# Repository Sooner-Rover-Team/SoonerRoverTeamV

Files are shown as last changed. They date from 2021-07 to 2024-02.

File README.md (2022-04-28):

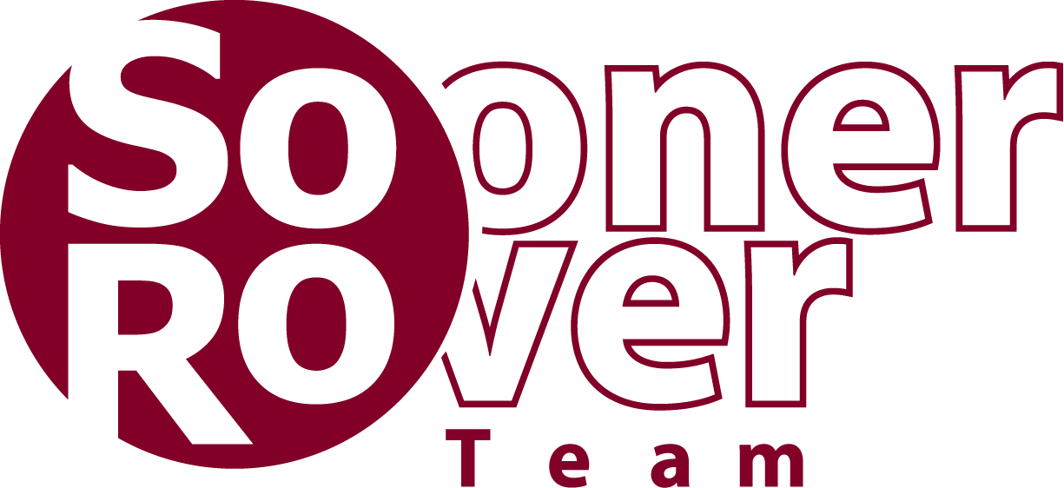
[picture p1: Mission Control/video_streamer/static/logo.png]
Sooner Rover Team Logo


---

This is the current code repository for the Sooner Rover Team.

## Active Tasks
[CS Tasks](https://github.com/bentonsmith8/SoonerRoverTeamV/projects/2)

[Electrical Tasks](https://github.com/bentonsmith8/SoonerRoverTeamV/projects/3)

## Previous Repo
[Link to the SoRo-19-20 Repo](https://github.com/eric-plus-plus/SoRo-19-20)

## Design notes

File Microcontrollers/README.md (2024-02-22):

# Microcontrollers
This folder contains all microcontroller code that has been used on SORO in the past. Some examples are provided for testing. The current implementation is in the Teensy 4.1 folder.

## Message Structures
### UDP
Mission Control sends UDP msgs to Ebox, which can also send CAN msgs to Arm/Science. UDP sends byteArrays, so assume each value is 0-255
- To Wheels = [0x01, 0x01, wheel0, wheel1, wheel2, wheel3, wheel4, wheel5, checkSUm]
- To LEDs = [0x01, 0x02, r, g, b, checkSum]
- To Arm = [0x02, bicep, foreArm, base, wristPitch, wristRotate, claw, checkSum]
- To Science = [0x03, bigAct, smallAct, testTubeAct, drill, servoCam, checkSum]
### CAN
Teensy microcontrollers communicate with each other via CAN (Ebox, 2 Arm and 1 Science). ID of CAN msg sets priority, meaning ID=0x03 has to wait for ID=0x01 to finish sending messages on the bus
- To lowerArm: ID = 0x01
- To upperArm: ID = 0x02
- To Science: ID = 0x03
- Back to Ebox = 0x04

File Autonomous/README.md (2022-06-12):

# Autonomous Code
This folder contains all of the code needed for the autonomous program to run. We tied for 2nd in the 2022 autonomous course with this code when one of our wheels wasn't moving!

## Dependencies
Requires `opencv-contrib-python` to be installed
Run `pip3 install .` in this folder <br>

## Running
First, ensure that `main.py` drives to the desired ArUco markers <br>
To run the main autonomous program without awful debugging output, enter
`python3 main.py <camera_file> 2> /dev/null` <br>
* To get the camera file, enter `v4l2-ctl --list-devices` to find the desired camera's file. It will look like `/dev/video2` <br>
<br>
To view the rover's location and get coordinates, navigate to &lt;rover's ip&gt;:5000 in your web browser

## Code Structure
### main.py
This is the program that gets run. This program allows the user to enter in GPS coordinates and then drives to the specified tags with -1 being given for a waypoint with no tag.

### Drive.py
The Drive class gives the user the ability to travel to a set of GPS locations while looking for a tag and then track either a tag or a gatepost after they've been seen.

### Location.py
API for using the GPS. Has methods that allows us to easily get the rover's heading and find how far the rover is from a set of GPS coordinates.

### UDPOut.py
Functions that allows the autonomous code to easily communicate to the MBed to control the wheels and LEDs.

### ARTracker.py
Class that gives the rover the ability to see ArUco markers and gets the rover's angle and distance from them. Also has the ability to utilize YOLO for the same purpose if the environment is properly setup.

### findFocalLength.py
Run this program directly to figure out the FOCAL_LENGTH parameters in config.ini

### gps
This folder contains the code needed to talk to the Swift GPS modules. I don't recommend going in here.

### runAutonomous.sh
Depricated. Can probably delete this but keeping it incase y'all ever go back to using three cameras

## Previous Code
Link to old, c++ autonomous code: https://github.com/eric-plus-plus/SoRo-19-20/tree/master/Autonomous

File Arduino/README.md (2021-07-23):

# Arduino Code :100:

Required libraries (install them from the built in library manager):
* EtherCard (1.1.0)
  * Only needed for using the Arduino Nano ethernet shield. The Uno-style shield (on the Megas) uses the built in ethernet library.
  * [GitHub](https://github.com/njh/EtherCard)

The "capstone arm" folder is full of other Arduino programs that were indended for the belt driven arm we did not end up using.

## Testing Programs

### servo_test.ino

This program is good for calibrating/testing a single talon (our motor controller).
To use it, change `#define PIN_SERVO 31` to whatever Arduino pin you're connecting the signal wire to, upload the code, and then open the serial monitor.
When you send a number to the Arduino it will write it to the servo.
When calibrating, use the range 10 to 170 instead of the full 0 to 180 because it freaks out the talons. 90 degrees will be still.

## Rover Programs

### wheel_controller.ino

This should be uploaded to the Arduino Nano in the e-box. The macro `#define DEBUG_MODE 0` can enable serial debugging messages. Don't use this when running the rover because it can cause the Arduino to randomly reset.

### arm_controller.ino

This is the code for the Arduino Nano controlling the currently used arm (the one with linear actuators). Like the wheel controller, it also has the optional debug macro.

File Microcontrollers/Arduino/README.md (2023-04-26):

# Arduino Code :100:

### mostRecent
    contains the arduino code that was last used on the rover before switching to Teensy.

### past_code 
    contains any program someone has made in the past for arduino that is no longer in use.

### examples 
    contains test scripts designed to make testing motors and arduino accessories easy.

Required libraries (install them from the built in library manager):
* EtherCard (1.1.0)
  * Only needed for using the Arduino Nano ethernet shield. The Uno-style shield (on the Megas) uses the built in ethernet library.
  * [GitHub](https://github.com/njh/EtherCard)

<!-- ## Testing Programs

### servo_test.ino

This program is good for calibrating/testing a single talon (our motor controller).
To use it, change `#define PIN_SERVO 31` to whatever Arduino pin you're connecting the signal wire to, upload the code, and then open the serial monitor.
When you send a number to the Arduino it will write it to the servo.
When calibrating, use the range 10 to 170 instead of the full 0 to 180 because it freaks out the talons. 90 degrees will be still.

## Rover Programs

### wheel_controller.ino

This should be uploaded to the Arduino Nano in the e-box. The macro `#define DEBUG_MODE 0` can enable serial debugging messages. Don't use this when running the rover because it can cause the Arduino to randomly reset.

### arm_controller.ino

This is the code for the Arduino Nano controlling the currently used arm (the one with linear actuators). Like the wheel controller, it also has the optional debug macro. -->

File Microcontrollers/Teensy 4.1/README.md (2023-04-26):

# Teensy
Teensy 4.1 microcontrollers are currently installed on REMI. They have a very high clock speed and built-in CAN tranceivers.

## REMI Setup
The teensyEBOX program receives UDP messages from the manual_operate.py program in MissionControl. Depending on the message contents, the teensy will either update wheel speeds/LEDs, or send CAN messages to the arm/ science package. The arm contains two teensy 4.1 microcontrollers so two CAN messages are sent to the arm at a time. The arm could be ran with one Teensy but eventually encoders will be added which could lead to input delay.

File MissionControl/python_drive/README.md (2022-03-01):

# manual_operate

This code can drive the rover, move the arm, and operate the science package.

## Usage

The config.ini file must have the correct ip addresses of the microcontrollers.

Ebox MBED IP: 10.0.0.101
Ebox MBED Port: 1001
Arm Arduino IP: 10.0.0.102
Arm Arduino Port: 1002
Science Arduino IP: 10.0.0.103
Science Arduino Port: 1003

The controller configuration can also be adjusted as different axes will have different indicies depending on the system/controller.
Config **0** sets the dual sticks to axes 0-3 while the triggers are 4 and 5. Config **1** sets left axes to 0 and 1 with the left trigger set to 2. The right stick is set to 3 and 4 with the right trigger at 5. To figure out the mappings of the controller, run controllertester.py.

## Controls

There are two distinct modes in the program: drive and operate. Drive obviously just drives the wheels. Operate can be used to control either the science package or the arm, depending on which is installed (can be toggled by pressing **Select**). **B** switches between drive and operate.

### Drive

The rover drives with tank controls (**Left Stick** moves left wheels, **Right Stick** moves right wheels). The **Left Bumper** will only move the front wheels while the **Right Bumper** will only move the back wheels. This could be useful for getting the rover unstuck. **A** will just make the lights flash. 

### Arm

The arm is controlled with the help of the GUI. The **Left Stick** controls the point of the wrist in space and the actuators will automatically adjust their length to keep the wrist on that point. The **Right Stick** controls the tilt and rotation of the wrist. The operator must be careful not to overtwist the wrist as the cords can get tangled and disconnected if the wrist is rotated too far. **A** opens and closes the claw. **Left Trigger** rotates the base to the left while **Right Trigger** rotates the base to the right.

### Science Package

The Science package has 4 distinct controllable elements. The **Left Stick** moves the drill up and down in space. The **Right Stick** controls the speed of the drill. **Right Trigger** increases the speed of the vacuum while **Left Trigger** decreases it. **Left Bumper** rotates the carousel clockwise while **Right Bumper** rotates the carousel counterclockwise. **A** attempts to move the carousel one seventh of a rotation, but it is based on time elapsed and may not move the same amout each time.

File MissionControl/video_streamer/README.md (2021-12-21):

# RoverCam Python

The video streamer is written in python. It requires python3 version >=3.8.5, 4 libraries, and creation of a virtual environment.

## Setting Up A Virtual Environment

Linux only: install virtual environments with

```bash
sudo apt-get install python3-venv
```

Make sure you are in /SoRo-19-20/Mission Control/video_streamer/ then run

```bash
python3 -m venv .venv
```

This will create a new virtual environment in /video_streamer/. The virtual environment must be activated every time the program needs to be run which can be done with:

Linux:

```bash
source .venv/bin/activate
```

Windows (Powershell):

```powershell
.venv/Scripts/Activate.ps1
```

---

## Installing Packages

Next, these four packages need to be installed

- wheel
- imutils
- flask
- opencv-contrib-python

install these with

```bash
python3 -m pip install wheel opencv-contrib-python flask
```

The imutils package needs to be installed after wheel:

```bash
python3 -m pip install imutils
```

---

## Usage

To run, use

```bash
python3 client.py -i [ip of the device] -o [port] --resolution "{width}x{height}" --source 1,2,3
```

and navigate to that ip from another device.

### Notes on Usage

The program will automatically look for up to 10 cameras on launch, but only 3 simultaneous streams are supported for bandwidth considerations. Additionally, specific camera indices can be specified through an argument. 

The resolution of cameras can be set via an argument. The default resolution is 640 by 480 but any resolution can be set by passing in a string such as "1280x720". "max" can also be passed as a resolution to set the cameras to their maximum resolution. Recordings from each camera can be started and will be saved to ./recordings/recording.avi. The quality and framerate can both be adjusted during runtime.

Each stream can also be relaunched, which disposes of the current VideoCapture and VideoWriter object and creates new instances. This could be useful in case of a hardware error with a USB camera; the program can reaccess the camera without fully restarting. It also has the side effect of saving any recordings that had been captured up to that point in the execution.

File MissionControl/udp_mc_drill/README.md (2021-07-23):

# Drill Controller
 ## Bindings
 Actuator - Left stick Y axis

 Fan speed - A/B (South/East) buttons to accelerate and decelerate, 
 respectively

 Drill speed - X/Y (West/North) buttons to accelerate and decelerate, respectively

 Front triggers (left or right doesn't matter) - Reset fan speed

 Back triggers (left or right doesn't matter) - Reset drill speed

 Direction - Bound to DPad buttons. Up for 1, right for 2, released for 0.

 # Running without compiling
 There's a chance your system can just run the binary in `/target/release/drill_controller`

 If you cannot you need to...
 # Compile from source and run
 Following the steps on [the Rust-lang website](https://www.rust-lang.org/tools/install), 
 execute 

```shell
curl --proto '=https' --tlsv1.2 -sSf https://sh.rustup.rs | sh`
```

and do what it says to

Once rust is installed, you can execute `cargo run` from the `/udp_mc_drill` directory (the `Cargo.toml` file *must* be in the directory you execute `cargo run` from, which is why you need to be in `/udp_mc_drill` to run it).

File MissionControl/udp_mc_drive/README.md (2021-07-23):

# Remote Control
This is a newer remote control program written in Rust.
Rust was chosen with the hopes that dependency management would be way easier than the issues that Python created.

# Building - Requires Rust to be installed
To build the program, execute `$ cargo build --release`.
The binary will be placed in `./target/release/rover_controller`.
You can run that binary as normal or execute `$ cargo run` to build and run all in one step

# Running the prebuilt binary
This repository tracks the `target` directory as I develop and test the program. This means that there is a prebuilt binary in the target directory.
While building for development, the binary is built at `./target/debug/rover_controller`, so this location will always be the latest revision. `./target/release/rover_controller` includes a binary with some compiler optimizations and such, which may or may not be desirable. It's a better bet to run the executable in the `./target/debug/` directory because the executable in `./target/release/` will only be built if I remember to build it, and the `./target/debug/` directory will have the binary whether I remember or not.

# Configuration
The config file only needs a single line, in the format
`target=[ARDUINO_IP]:[PORT]`. If the config file is missing or malformed, a default will be used. This default is (as of v0.9.0) `target=192.168.1.101:1237`, which should work with the arduino as it stands at the time of writing.

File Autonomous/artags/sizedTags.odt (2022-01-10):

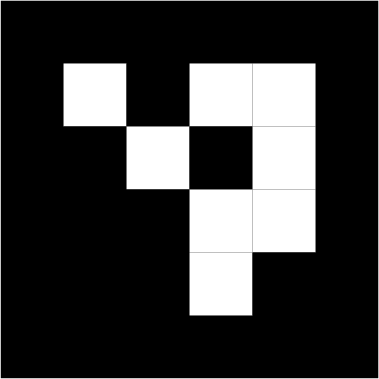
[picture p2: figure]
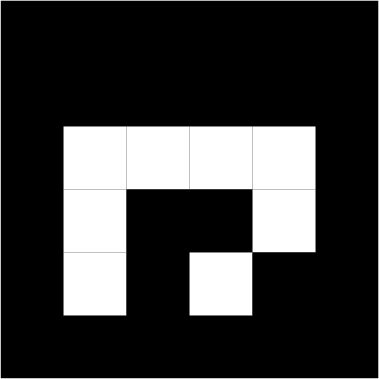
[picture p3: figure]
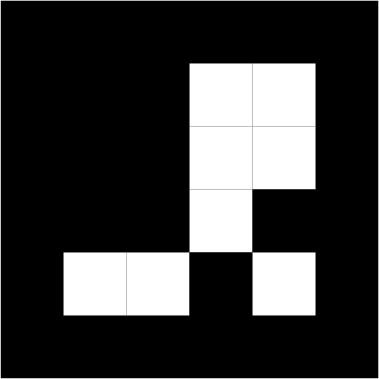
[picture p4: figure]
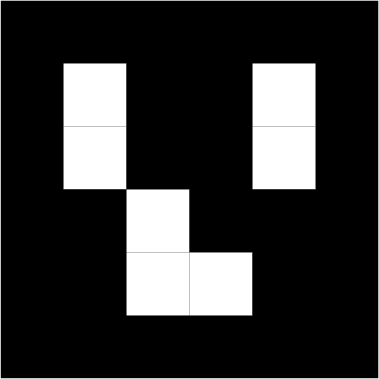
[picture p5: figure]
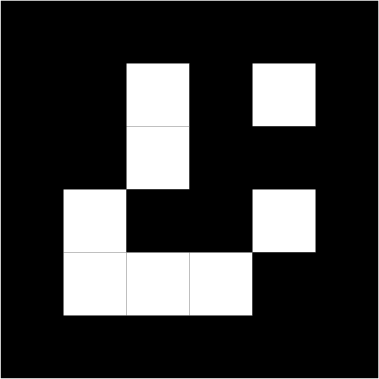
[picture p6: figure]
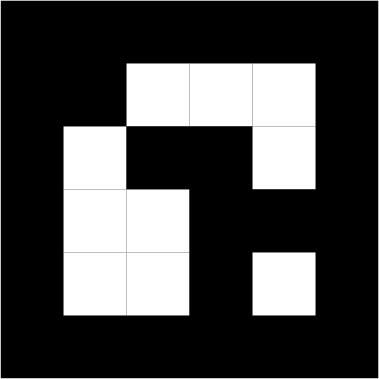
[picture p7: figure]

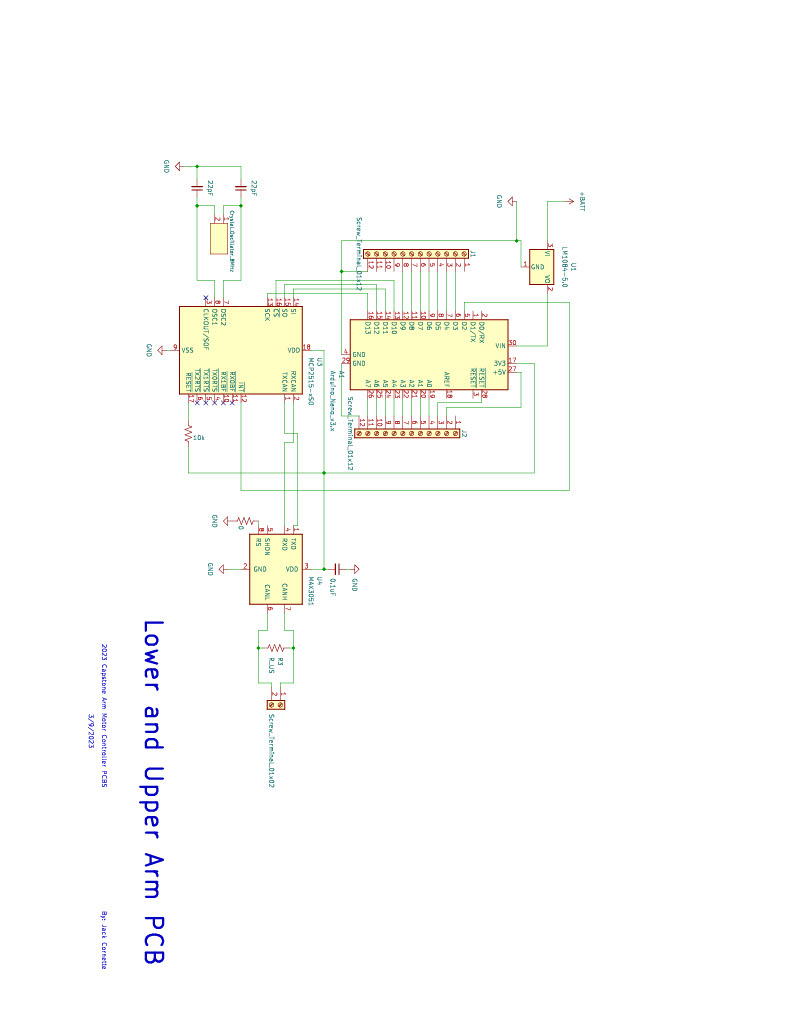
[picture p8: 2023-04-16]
PCB/Arm/lowerArm_upperArm/schematicPDF1024_1.jpg

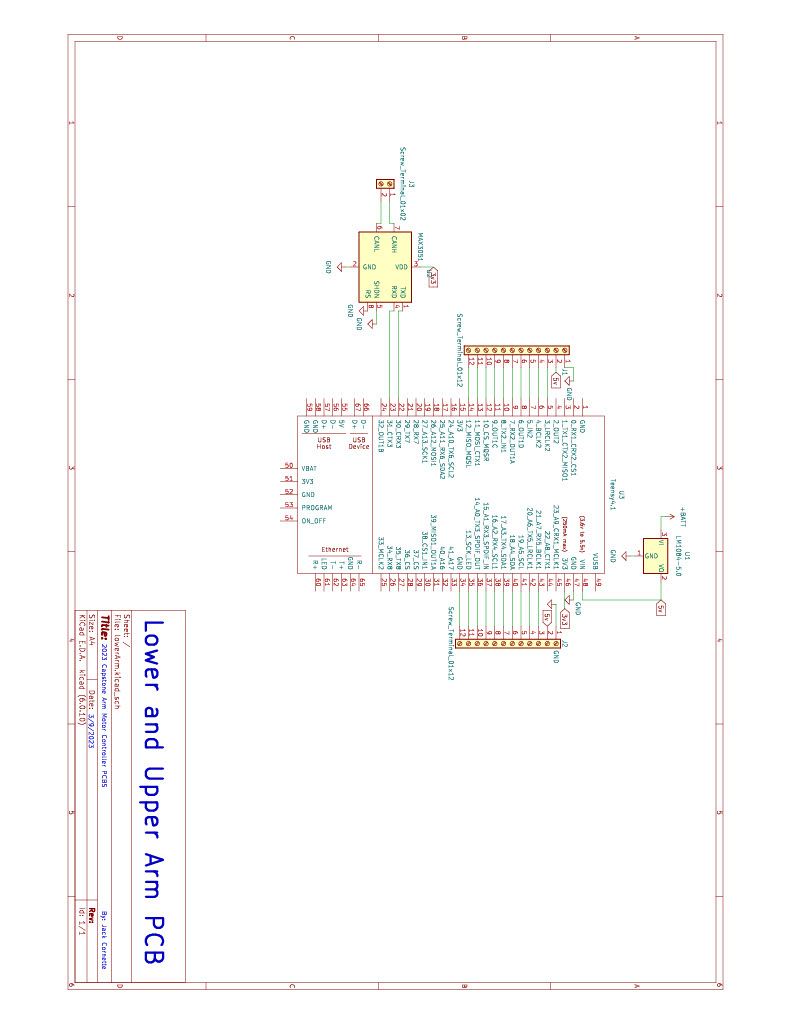
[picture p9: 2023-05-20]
PCB/Arm/teensyLowerUpperArm/schematic.jpg

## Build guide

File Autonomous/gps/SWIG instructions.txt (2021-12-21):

In order to run SWIG you must:
install swig
install python dev tools
make sure you have gcc/g++ installed
create interface files module.i

Process:
1. wrap edc.c into a library
2. use edc.c to wrap sbc.c into a library
3. use sbc.c to wrap gps.c into a library
4. Then use gps.c library to wrap main.c or main.cpp

=================REWRAPPING INSTRUCTIONS================
to wrap edc.c:

swig -python edc.i
gcc -fpic -c -I/usr/include/python3.8 edc.c edc_wrap.c
gcc -shared edc.o edc_wrap.o -o _edc.so
python3
import edc

----- It seems to work
============================================================================
to wrap sbp.c:

swig -python sbp.i
gcc -fpic -c -I/usr/include/python3.8 sbp.c sbp_wrap.c
gcc -shared sbp.o sbp_wrap.o -o _sbp.so edc.o 
python3
import sbp

---- It seems to work too, adds edc.o to the linking step so that it can get the edc functions
========================================================================================
To wrap gps.c:

swig -python gps.i
gcc -fpic -c -I/usr/include/python3.8 gps.c gps_wrap.c
gcc -shared gps.o gps_wrap.o -o _gps.so sbp.o edc.o
python3
import gps

--- Seems to work
==================================================================================
To wrap main.c:

swig -python main.i
gcc -fpic -c -I/usr/include/python3.8 main.c main_wrap.c
gcc -shared main.o main_wrap.o -o _gpsmain.so gps.o sbp.o edc.o
python3
import gpsmain
gpsmain.gpsmain()

--- Seems to work without the connection, though, just prints 0s for all the results
==========================================================================================

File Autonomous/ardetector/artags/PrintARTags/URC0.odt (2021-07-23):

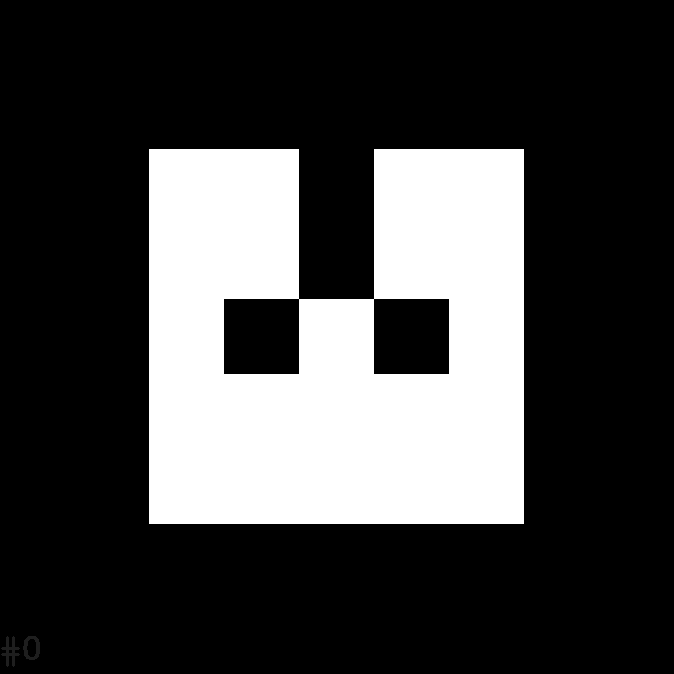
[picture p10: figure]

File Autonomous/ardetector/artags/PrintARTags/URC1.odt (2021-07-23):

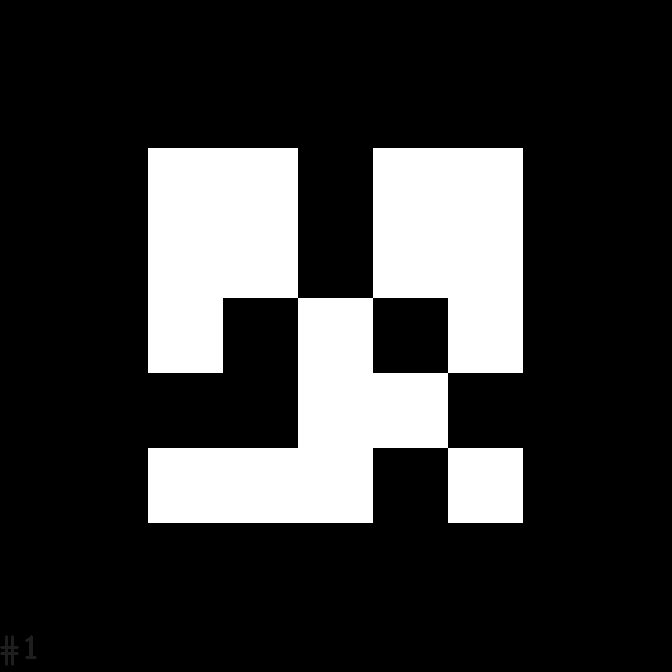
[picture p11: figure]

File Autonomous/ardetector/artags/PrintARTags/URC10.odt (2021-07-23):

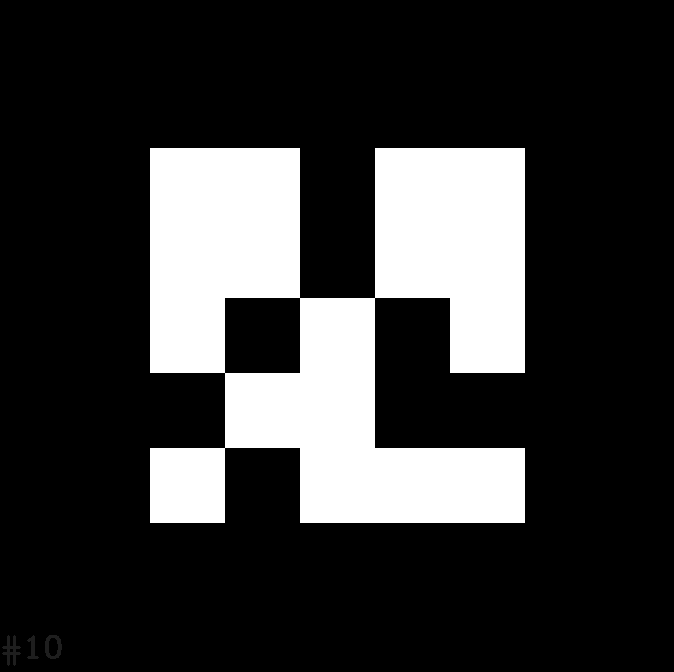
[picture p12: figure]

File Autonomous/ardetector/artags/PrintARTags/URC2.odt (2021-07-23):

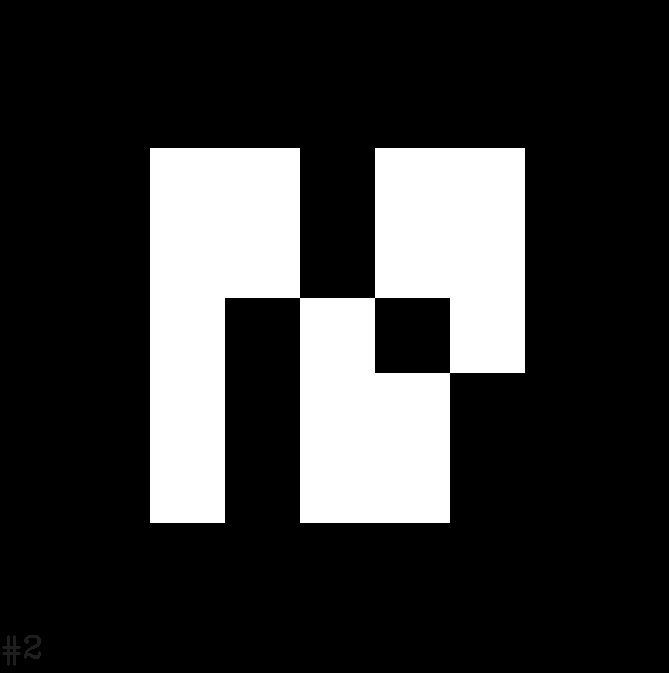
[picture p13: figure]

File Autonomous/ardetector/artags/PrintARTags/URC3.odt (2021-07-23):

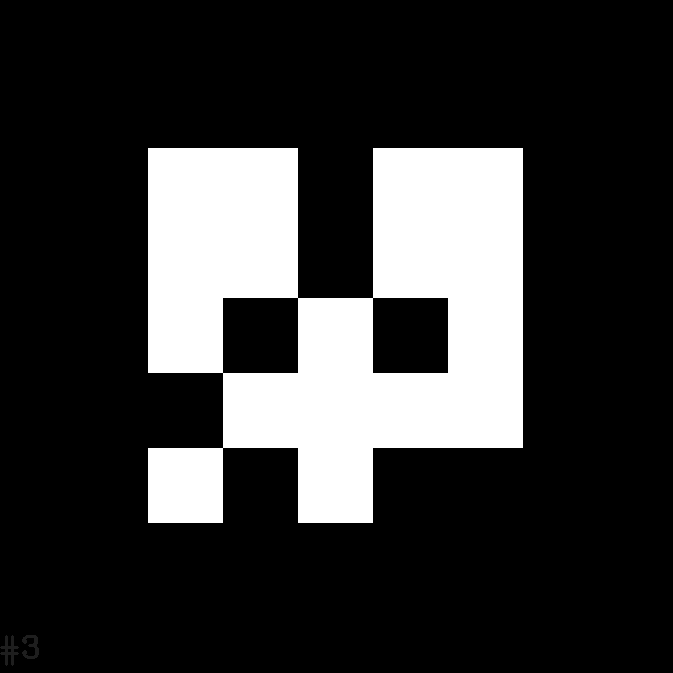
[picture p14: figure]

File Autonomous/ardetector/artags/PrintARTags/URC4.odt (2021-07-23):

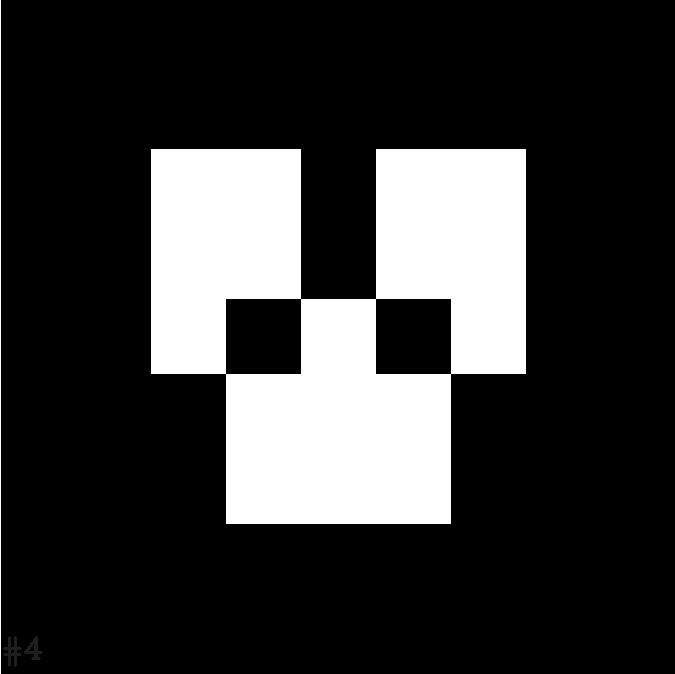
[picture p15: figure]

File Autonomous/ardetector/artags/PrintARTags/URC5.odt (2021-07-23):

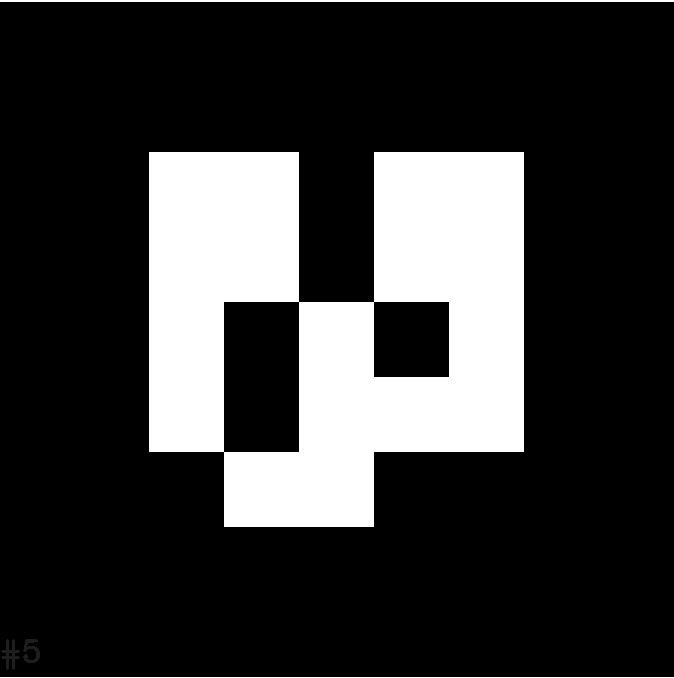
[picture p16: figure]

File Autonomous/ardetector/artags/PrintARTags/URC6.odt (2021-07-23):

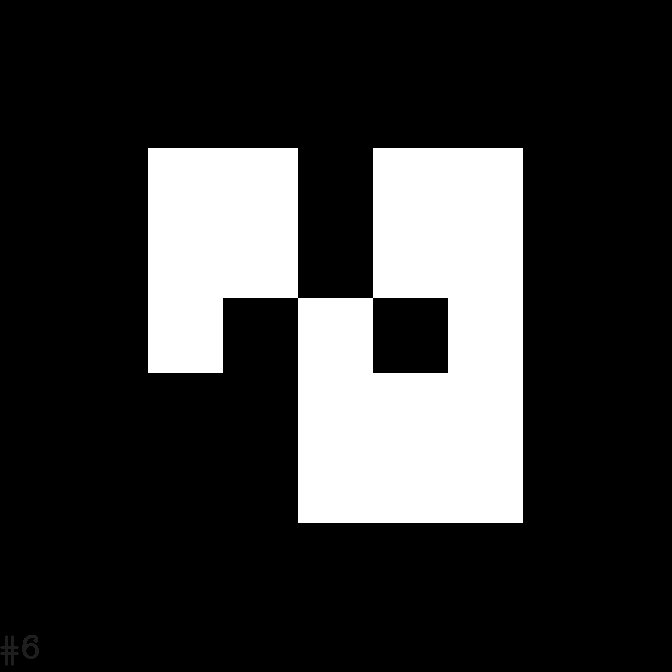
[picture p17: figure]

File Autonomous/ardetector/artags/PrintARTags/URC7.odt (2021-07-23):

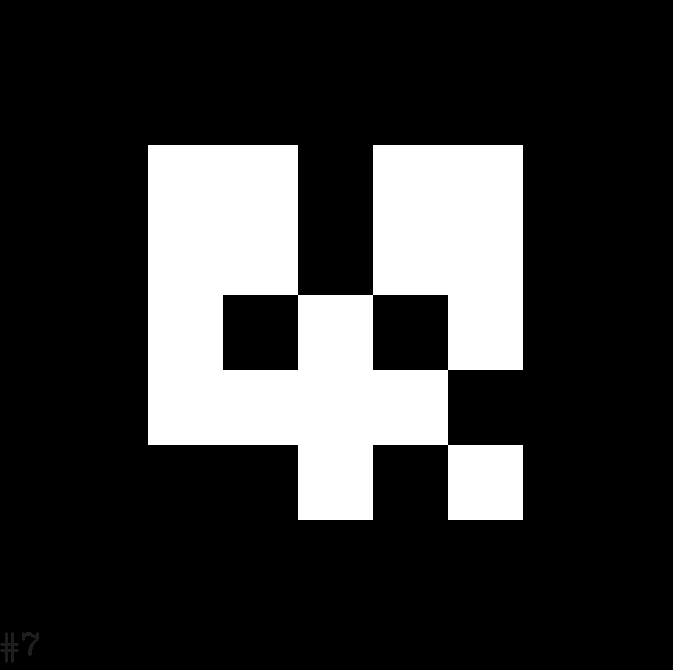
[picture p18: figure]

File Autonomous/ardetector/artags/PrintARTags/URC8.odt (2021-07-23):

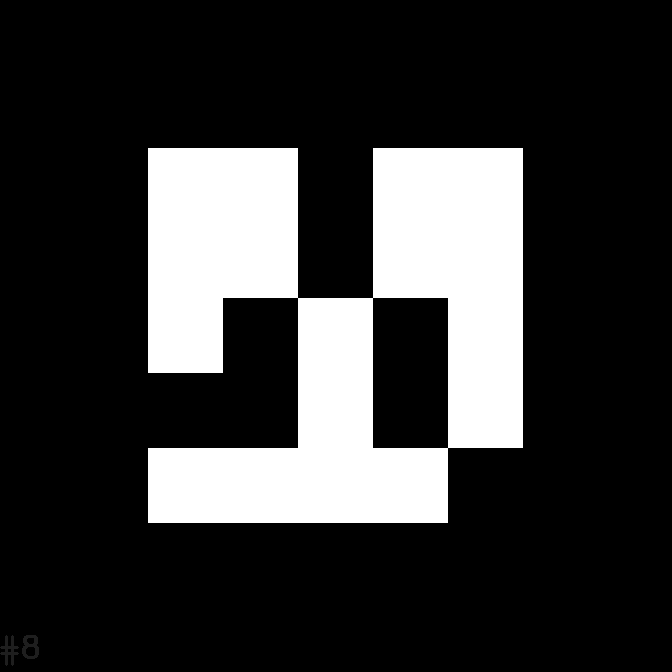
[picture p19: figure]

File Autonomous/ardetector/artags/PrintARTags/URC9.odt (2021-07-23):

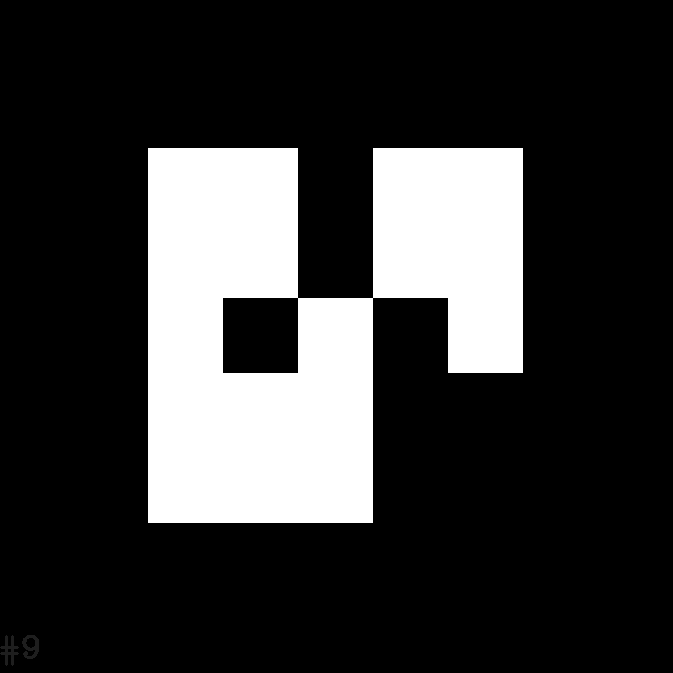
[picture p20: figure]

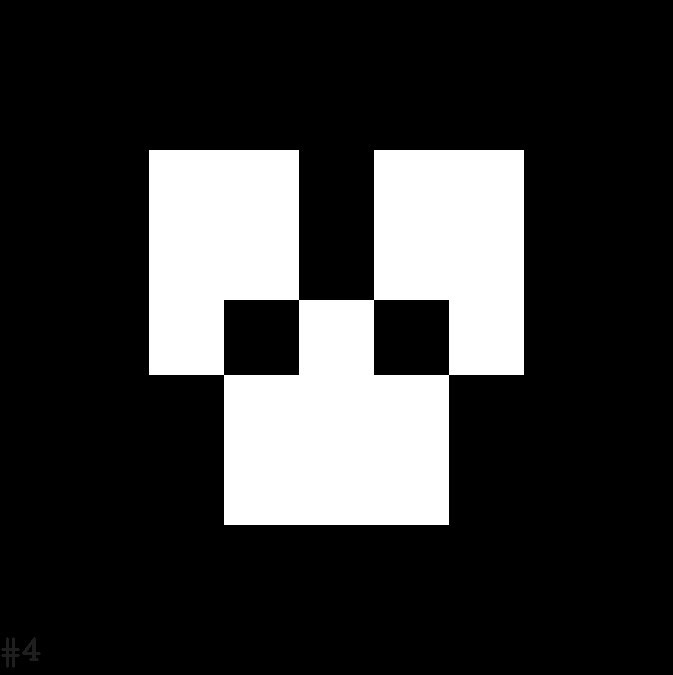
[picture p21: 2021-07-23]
Autonomous/ardetector/artags/PrintARTags/urc4cropped.png

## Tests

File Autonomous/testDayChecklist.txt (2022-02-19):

1. Make sure wheels turn
2. Connect to GPS
3. Find an ar tag
4. Leave 3 people at bay

Don't forget to bring:
1. Battery for e box
2. AR tags
3. First aid and fire extinguisher
4. Laptop

Don't forget to power cycle the GPS

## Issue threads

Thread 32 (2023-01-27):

BIG: Breaking everything into smaller repos

onkoe, 2023-01-27:
### What are we doing?
Currently, the Rover Team's repository is really... scary. Frankly, I'm not too sure how everyone got so much work done with this level of organization. Anyways, the plan is to fix the problems by organizing all of the different subdirectories that are sitting in this one repo. As needed, they will all become separate GitHub repos on the Sooner Rover Team org.

### How are we splitting everything up?
I'm deciding a rough draft below. You can use the command `tree` to easily look at the file structures. Use `tree -d` to see only directories (folders). When I see patterns of grouped utilities that are developed together, they'll stay as a group. Otherwise, they're getting stored or archived.

### How will it look?
Each of the listed items below will become their own split-off repo and project. The `(/foo)` represents its current location in the giant repo. There don't need to be any active maintainers, since our "human resources" are limited. That said, if something needs to be archived, let me know.  Also, this link on [moving files between repos](https://medium.com/@ayushya/move-directory-from-one-repository-to-another-preserving-git-history-d210fa049d4b) while preserving commit history will be *very* useful!

Anyways, I plan to have it look something like this:

#### Arduino
##### (/Arduino/)
This was a pretty easy split. This folder contains various Arduino files, all of which are related. Here's a folder listing:
```
Arduino/
├── arm_controller
├── arm_test
├── capstone_arm
│   ├── control_arm
│   ├── rover_arm
│   ├── rover_arm_pid_test
│   └── rover_arm_test
├── drill_controller
├── drill_test
├── servo_test
└── wheel_controller
```

#### YOLO/darknet
##### (/Autonomous/YOLO/darknet/)
This is a sizeable library whose source is just sitting in the middle of everything. It really needs its own repo. Here's a folder listing:
```
Autonomous/
├── YOLO
│   └── darknet
│       ├── 3rdparty
│       │   ├── pthreads
│       │   │   └── include
│       │   └── stb
│       │       └── include
│       ├── cfg
│       ├── cmake
│       │   └── Modules
│       ├── data
│       │   └── soro
│       ├── include
│       ├── scripts
│       │   ├── log_parser
│       │   └── windows
│       └── src
│           └── csharp
├── artags
│   └── old
│       └── PrintARTags
├── examples
├── gps
└── libs
```

#### MBED
##### (/MBED/)
MBED is a mixed bag for me. It includes many small projects that have connected goals. For this reason, I'm not sure if I want to put each project in its own repo, do that but with submodules, or just keep everything together. For now, I'll just say it belongs together. Here's a listing (it's so small that you can put files too):
```
MBED
├── EBoxMBED
│   └── main.cpp
├── README.md
├── SPItoCANRead
│   └── main.cpp
├── SPItoCANSend
│   └── main.cpp
├── UDPSocket
│   └── main.cpp
└── WheelMBED
    └── main.cpp
```

#### RoverMap
##### (/Mission Control/RoverMap/)
To be honest, even after studying the README, I'm not sure if these are two separate projects (frontend and backend) or if they both require each other. For now, let's keep them together. Here's a directory listing:
```
RoverMap/
├── RoverMapTileGenerator
├── example
└── frontend
    └── leaflet
        └── images
```
(frontend is a whole web interface. but it's a lil guy)

#### python_drive
##### (/Mission Control/python_drive/)
This project is completely distinct from the rest of everything. It controls the vehicle! Here's a short file listing:
```
python_drive/
├── README.md
├── config.ini
├── controllertester.py
├── manual_operate.py
└── util.py
```

#### video_streamer
##### (/Mission Control/video_streamer/)
The video_streamer project has a lot of documentation! I think it would be well off in its own repo, along with a detailed INSTALLATION.md and reduced README.md. Here's a file listing:
```
video_streamer/
├── README.md
├── client.py
├── config.ini
├── static
│   └── logo.png
├── templates
│   └── index.html
├── utils.py
└── videostream.py
```

### TO ARCHIVE
- udp_mc_drill and udp_mc_drive **(/Mission Control/udp_mc_dr\*\*\*)**
    - According to the Mission Control README, both of these are useless and have been replaced with a modern Python script.
    - It's sad to get rid of the only Rust projects, but necessary :(

### And..?
With that, we're done! All of the files in the Sooner Rover Team's modern repo have been accounted for! I think it would be also wise to make a **Junkyard** repo that acts as a place to store archived projects that are pretty old/small. If you have any suggestions or changes I should make, please let me know!

### Complete

- [ ] Arduino
- [ ] darknet
- [ ] MBED
- [ ] RoverMap
- [ ] python_drive
- [ ] video_streamer
- [ ] Graveyard
    - [ ] udp_mc_drill
    - [ ] udp_mc_drive
    - [x] my rusty dreams :(

bentonsmith8, 2023-01-27:
I like the breakdown for the most part. A few things can be moved around even more such as capstone_arm which hasn't been used in years and can go into the graveyard. Also we'll still need a repo for the autonomous code itself (stuff in gps, libs, and examples).

cwealeft, 2023-01-27:
<!--
/* Font Definitions */
@font-face
	{font-family:"Cambria Math";
	panose-1:2 4 5 3 5 4 6 3 2 4;}
@font-face
	{font-family:Calibri;
	panose-1:2 15 5 2 2 2 4 3 2 4;}
@font-face
	{font-family:"Amasis MT Pro";
	panose-1:2 4 5 4 5 0 5 2 3 4;}
/* Style Definitions */
p.MsoNormal, li.MsoNormal, div.MsoNormal
	{margin:0in;
	font-size:11.0pt;
	font-family:"Calibri",sans-serif;}
a:link, span.MsoHyperlink
	{mso-style-priority:99;
	color:blue;
	text-decoration:underline;}
.MsoChpDefault
	{mso-style-type:export-only;}
@page WordSection1
	{size:8.5in 11.0in;
	margin:1.0in 1.0in 1.0in 1.0in;}
div.WordSection1
	{page:WordSection1;}
-->The arm capstone is current though… Christine WealeSenior, El.Eng. Junior, OUVP of Service, Alpha Phi OmegaUG Research Asst. | RIL From: Benton SmithSent: Friday, January 27, 2023 12:47To: Sooner-Rover-Team/SoonerRoverTeamVCc: SubscribedSubject: Re: [Sooner-Rover-Team/SoonerRoverTeamV] BIG: Breaking everything into smaller repos (Issue #32) I like the breakdown for the most part. A few things can be moved around even more such as capstone_arm which hasn't been used in years and can go into the graveyard. Also we'll still need a repo for the autonomous code itself (stuff in gps, libs, and examples).—Reply to this email directly, view it on GitHub, or unsubscribe.You are receiving this because you are subscribed to this thread.Message ID: ***@***.***> 

bentonsmith8, 2023-01-28:
As far as I can tell, all of the code in that folder is from the OLD arm capstone from 4-5 years ago. I'm not sure if any of it applies since that one worked very differently to the arm that we currently use on the rover.

onkoe, 2023-01-28:
Is graveyarding this the consensus? I'm happy to start working on moving everything, and of course, we can always revert and move the *capstone_arm* project somewhere else if it's deemed necessary.

bentonsmith8, 2023-01-29:
Yeah, I like the idea of just throwing everything obsolete in a repo by itself so it's not in the way of the useful stuff but we have access to it if we need it.

ROMANT21, 2023-02-25:
For the Autonomous Folder, I would say that you could move the YOLO folder into a sub-repo. Other than that, I give it a green light.

onkoe, 2023-02-25:
dont touch til march 4th :)

onkoe, 2023-06-24:
Note: `MBED` was dissolved into `Microcontrollers` with fd11b43. `Arduino` was also moved.

In the future, please explicitly commit for moves like this - it's hard to keep track! Squash merges are a little scary ;)

onkoe, 2023-06-24:
Also moved:
- [x] Discord Bot
- [x] PCB
    - This seems to be a CAD backup repo. GitHub doesn't like that, and `git` isn't designed for it. It's best to remove this repo ASAP!

I now need to apply the MIT license to each of the moved repos. Let's keep track:
- [ ] pcb
- [ ] discord_bot
- [ ] Autonomous
- [ ] gps
- [ ] rovercam-python
- [ ] python_drive
- [ ] RoverMap
- [ ] YOLO (wish we'd have kept it WTFPL ;) )
- [ ] Microcontrollers
- [ ] soro-documentation

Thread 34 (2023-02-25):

main.py (and others): Move Try Statements to Result

onkoe, 2023-02-25:
In almost all Python projects, `try` statements are used to handle errors. However, they act as `:GOTO` statements, and I'd like to avoid them in any important project files.

The modern replacement for try statements is to use the `Result` type in Rust. But since we're in Python, we'd need to use a Result implementation, such as... [result](https://pypi.org/project/result/).

## Motivations
`Result` forces you to:

- handle your errors
- cover all potential cases
- deal with errors without interrupting control flow

It fixes some issues from `try`, such as:

- jumping between flow paths
- not handling errors correctly
- having confusing, unmaintainable error handling

In other words, even with very little understanding, programmers become nearly perfect in almost all error handling situations. Migrating to `result` from `try` is a worthy cause that will lead to improved error handling and better maintainability.

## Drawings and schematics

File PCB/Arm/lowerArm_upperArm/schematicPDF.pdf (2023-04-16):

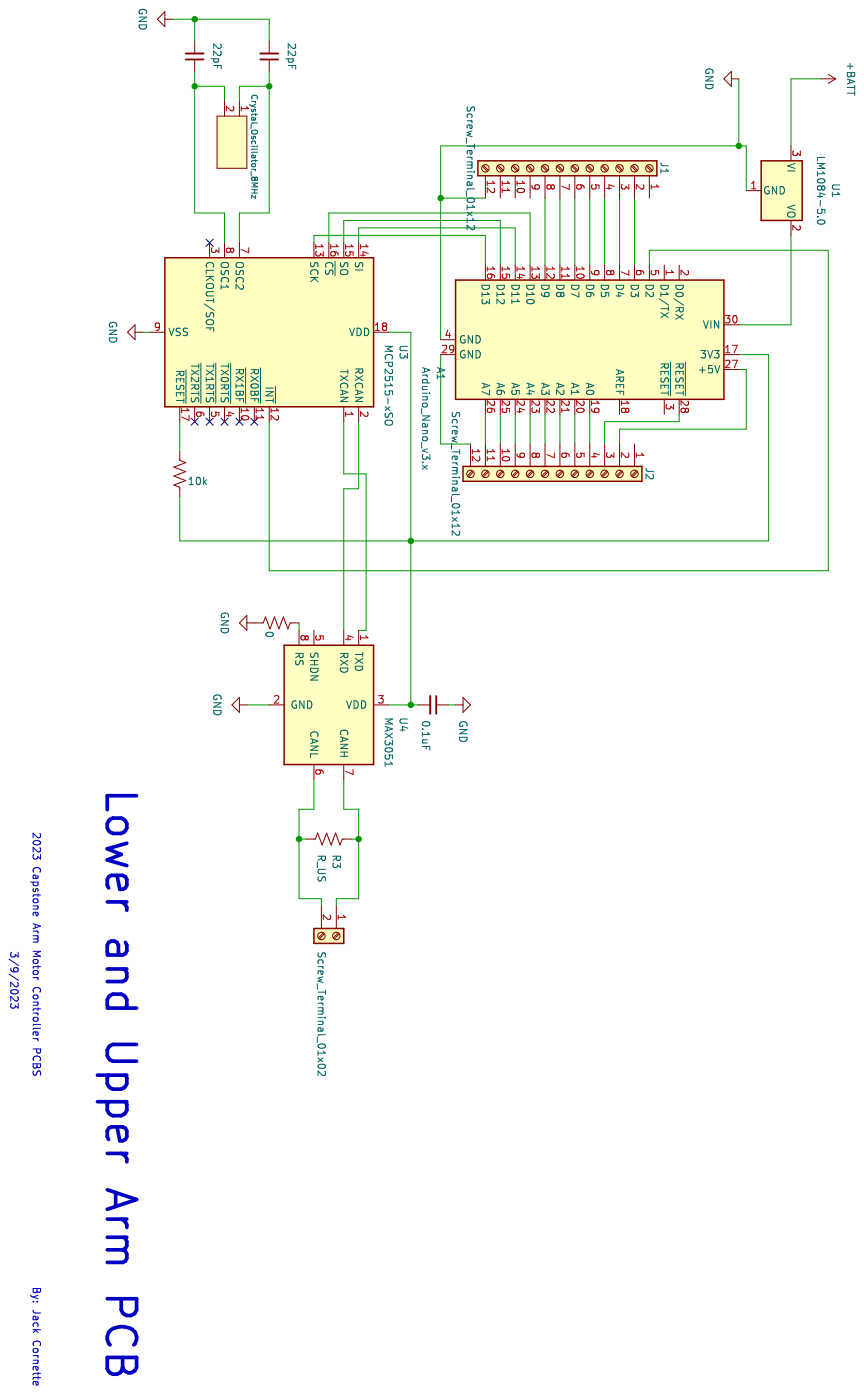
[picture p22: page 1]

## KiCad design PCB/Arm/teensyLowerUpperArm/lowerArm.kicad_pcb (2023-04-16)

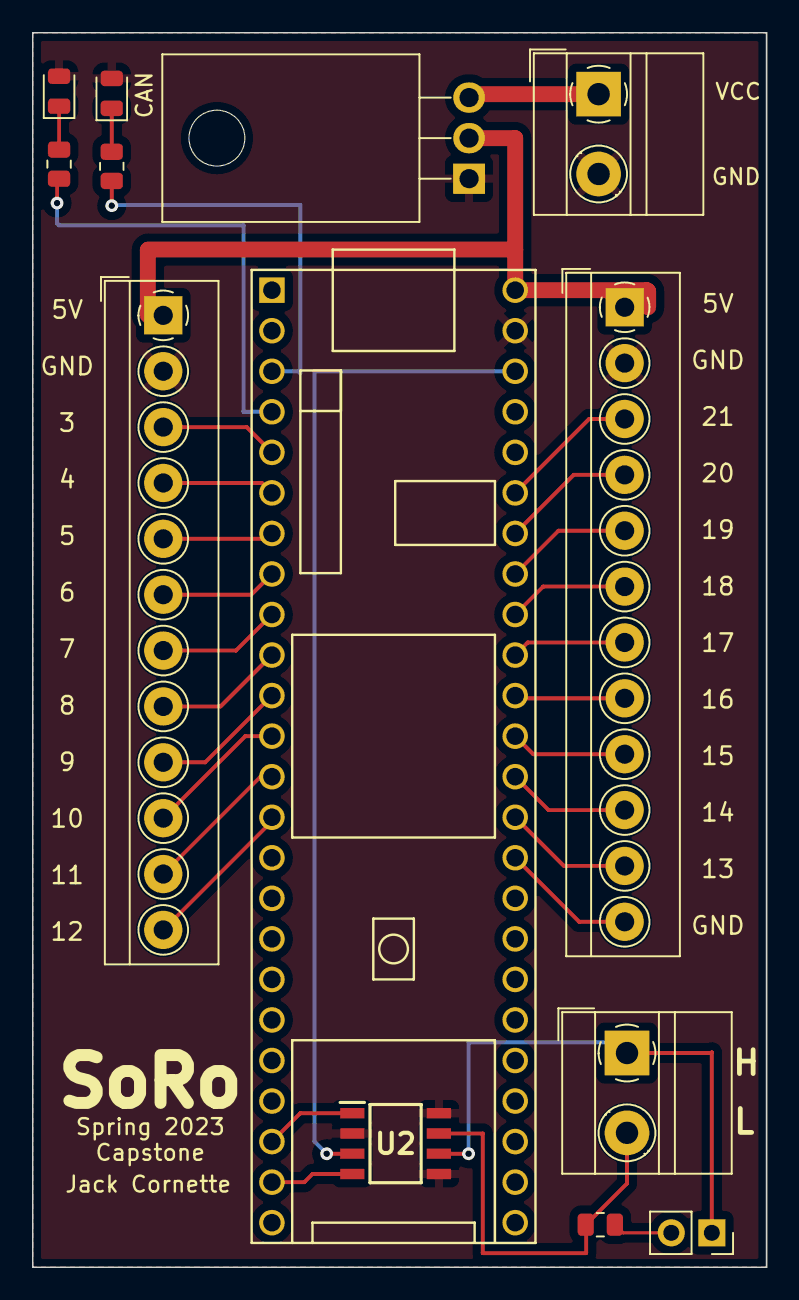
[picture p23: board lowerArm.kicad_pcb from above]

Board: 2 copper layers, 46.0 x 77.3 mm, 11 parts (0 on the bottom side), 28 nets.

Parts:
CAN: LED_0805_2012Metric
J1, J2: Screw_Terminal_01x12; TerminalBlock_4Ucon_1x12_P3.50mm_Horizontal
J3, J3#2: Screw_Terminal_01x02; TerminalBlock_MetzConnect_Type011_RT05502HBWC_1x02_P5.00mm_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
R3, R3#2, R3#3: R_US; R_0805_2012Metric
U1: LM1084-5.0; TO-220F-3_Horizontal_TabDown
U2: MAX3051; SOIC127P600X175-8N
U3: Teensy4.1; Teensy41_pinHeadOnly

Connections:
3v3: U2.3 (VDD), U3.46 (3V3)
5v: J1.1, J2.1, U1.2 (VO), U3.48 (VIN)
+BATT: J3.1, U1.3 (VI)
GND: CAN.2, J1.2, J2.2, J3.2, U1.1 (GND), U2.2 (GND), U2.5 (SHDN), U2.8 (RS), U3.47 (GND)
unnamed: J1.3, U3.5 (3_LRCLK2)
unnamed: J1.4, U3.6 (4_BCLK2)
unnamed: J1.5, U3.7 (5_IN2)
unnamed: J1.6, U3.8 (6_OUT1D)
unnamed: J1.7, U3.9 (7_RX2_OUT1A)
unnamed: J1.8, U3.10 (8_TX2_IN1)
unnamed: J1.9, U3.11 (9_OUT1C)
unnamed: J1.10, U3.12 (10_CS_MQSR)
unnamed: J1.11, U3.13 (11_MOSI_CTX1)
unnamed: J1.12, U3.14 (12_MISO_MQSL)
unnamed: J2.3, U3.43 (21_A7_RX5_BCLK1)
unnamed: J2.4, U3.42 (20_A6_TX5_LRCLK1)
unnamed: J2.5, U3.41 (19_A5_SCL)
unnamed: J2.6, U3.40 (18_A4_SDA)
unnamed: J2.7, U3.39 (17_A3_TX4_SDA1)
unnamed: J2.8, U3.38 (16_A2_RX4_SCL1)
unnamed: J2.9, U3.37 (15_A1_RX3_SPDIF_IN)
unnamed: J2.10, U3.36 (14_A0_TX3_SPDIF_OUT)
unnamed: J2.11, U3.35 (13_SCK_LED)
unnamed: J2.12, U3.34 (GND)
unnamed: J3#2.2, R3#2.1, U2.7 (CANH)
unnamed: J3#2.1, U2.6 (CANL)
unnamed: U2.1 (TXD), U3.22 (30_CRX3)
unnamed: U2.4 (RXD), U3.23 (31_CTX3)

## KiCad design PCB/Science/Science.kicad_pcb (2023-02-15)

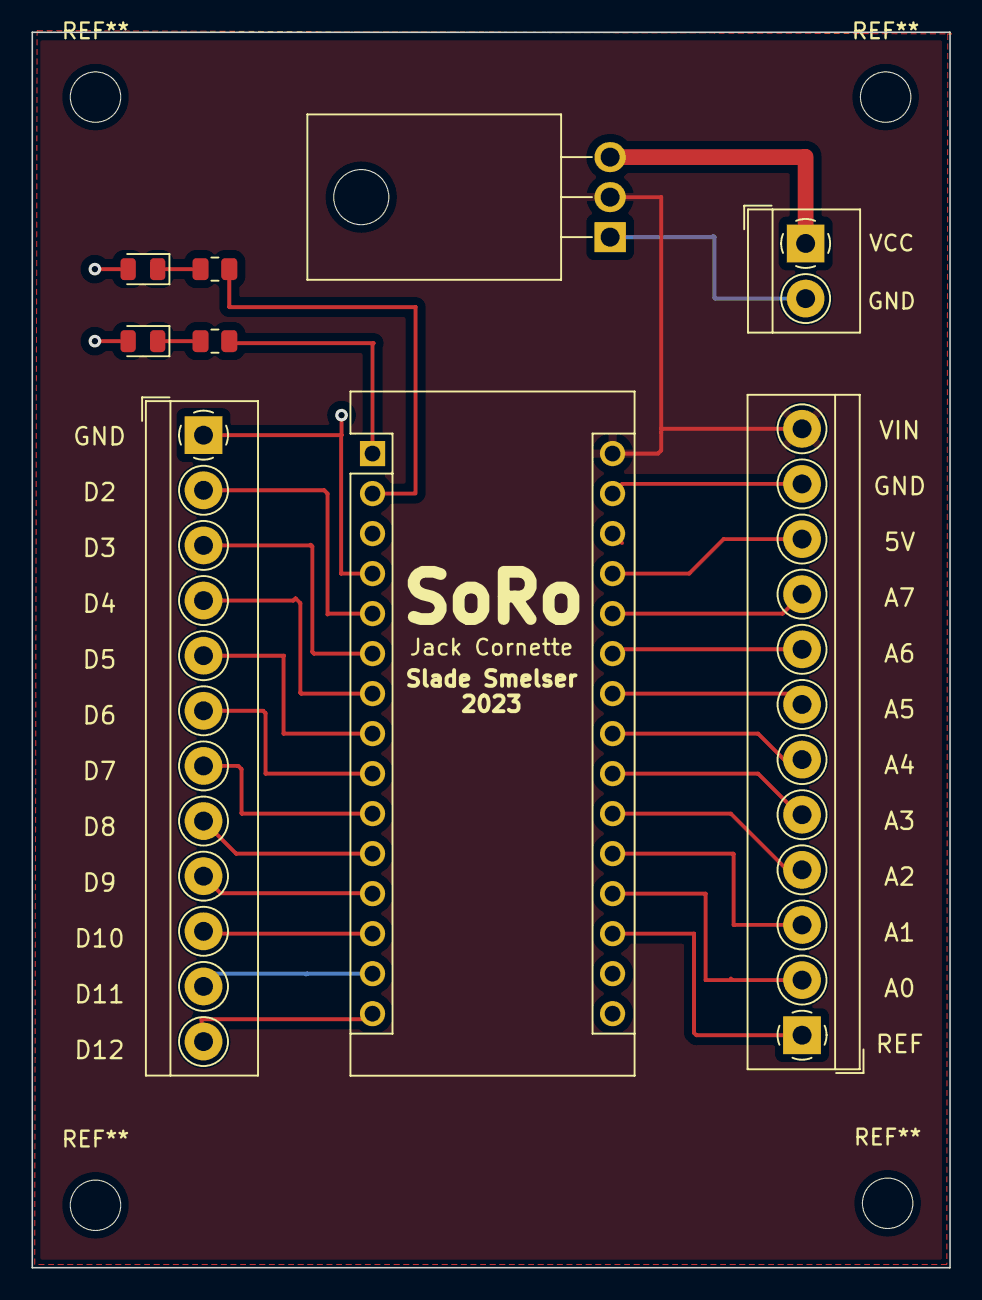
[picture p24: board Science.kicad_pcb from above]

Board: 2 copper layers, 58.3 x 78.4 mm, 8 parts (0 on the bottom side), 20 nets.

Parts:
A1: Arduino_Nano_v3.x; Arduino_Nano
CAN: LED_0805_2012Metric
J1, J2: Screw_Terminal_01x12; TerminalBlock_4Ucon_1x12_P3.50mm_Horizontal
J3: Screw_Terminal_01x02; TerminalBlock_4Ucon_1x02_P3.50mm_Horizontal
R3, R3#2: R_US; R_0805_2012Metric
U1: LM1084-5.0; TO-220F-3_Horizontal_TabDown

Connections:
+BATT: J3.1, U1.3 (VI)
GND: A1.4 (GND), CAN.2, J1.1, J3.2, U1.1 (GND)
unnamed: A1.6 (D3), J1.3
unnamed: A1.7 (D4), J1.4
unnamed: A1.8 (D5), J1.5
unnamed: A1.9 (D6), J1.6
unnamed: A1.12 (D9), J1.9
unnamed: A1.13 (D10), J1.10
unnamed: A1.15 (D12), J1.12
unnamed: A1.19 (A0), J2.2
unnamed: A1.20 (A1), J2.3
unnamed: A1.21 (A2), J2.4
unnamed: A1.22 (A3), J2.5
unnamed: A1.23 (A4), J2.6
unnamed: A1.24 (A5), J2.7
unnamed: A1.25 (A6), J2.8
unnamed: A1.26 (A7), J2.9
unnamed: A1.27 (+5V), J2.10
unnamed: A1.29 (GND), J2.11
unnamed: A1.30 (VIN), J2.12, U1.2 (VO)

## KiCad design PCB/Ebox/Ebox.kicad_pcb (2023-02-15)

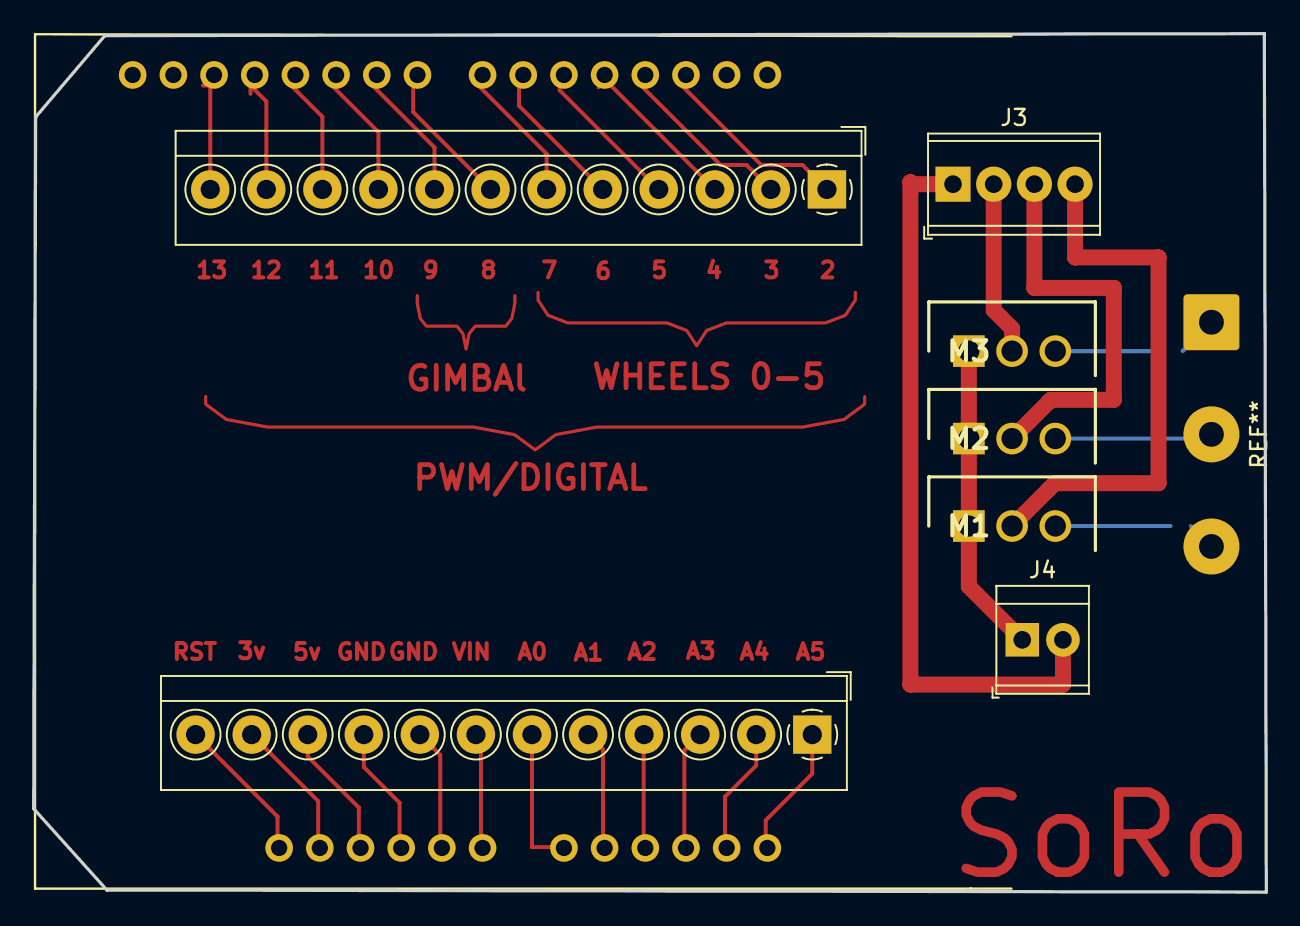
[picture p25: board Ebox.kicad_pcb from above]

Board: 2 copper layers, 77.0 x 53.6 mm, 8 parts (0 on the bottom side), 29 nets.

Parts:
J1, J2: Screw_Terminal_01x12; TerminalBlock_4Ucon_1x12_P3.50mm_Horizontal
J3: Screw_Terminal_01x04; TerminalBlock_Phoenix_MPT-0,5-4-2.54_1x04_P2.54mm_Horizontal
J4: Screw_Terminal_01x02; TerminalBlock_TE_282834-2_1x02_P2.54mm_Horizontal
M1, M2, M3: MNMOS; TO270P460X1020X2008-3P
XA1: Arduino_Mega2560_Shield

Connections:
unnamed: J1.1, XA1.D2 (D2_INT0)
unnamed: J1.2, XA1.D3 (D3_INT1)
unnamed: J1.3, XA1.D4
unnamed: J1.4, XA1.D5
unnamed: J1.5, XA1.D6
unnamed: J1.6, XA1.D7
unnamed: J1.7, XA1.D8
unnamed: J1.8, XA1.D9
unnamed: J1.9, XA1.D10
unnamed: J1.10, XA1.D11
unnamed: J1.11, XA1.D12
unnamed: J1.12, XA1.D13
unnamed: J2.1, XA1.A5
unnamed: J2.2, XA1.A4
unnamed: J2.3, XA1.A3
unnamed: J2.4, XA1.A2
unnamed: J2.5, XA1.A1
unnamed: J2.6, XA1.A0
unnamed: J2.7, XA1.VIN
unnamed: J2.8, XA1.GND3 (GND)
unnamed: J2.9, XA1.GND2 (GND)
unnamed: J2.10, XA1.5V1 (5V)
unnamed: J2.11, XA1.3V3 (3.3V)
unnamed: J2.12, XA1.RST1 (RESET)
unnamed: J3.1, J4.2
unnamed: J3.2, M3.2 (G)
unnamed: J3.3, M2.2 (G)
unnamed: J3.4, M1.2 (G)
unnamed: J4.1, M1.1 (D), M2.1 (D), M3.1 (D)

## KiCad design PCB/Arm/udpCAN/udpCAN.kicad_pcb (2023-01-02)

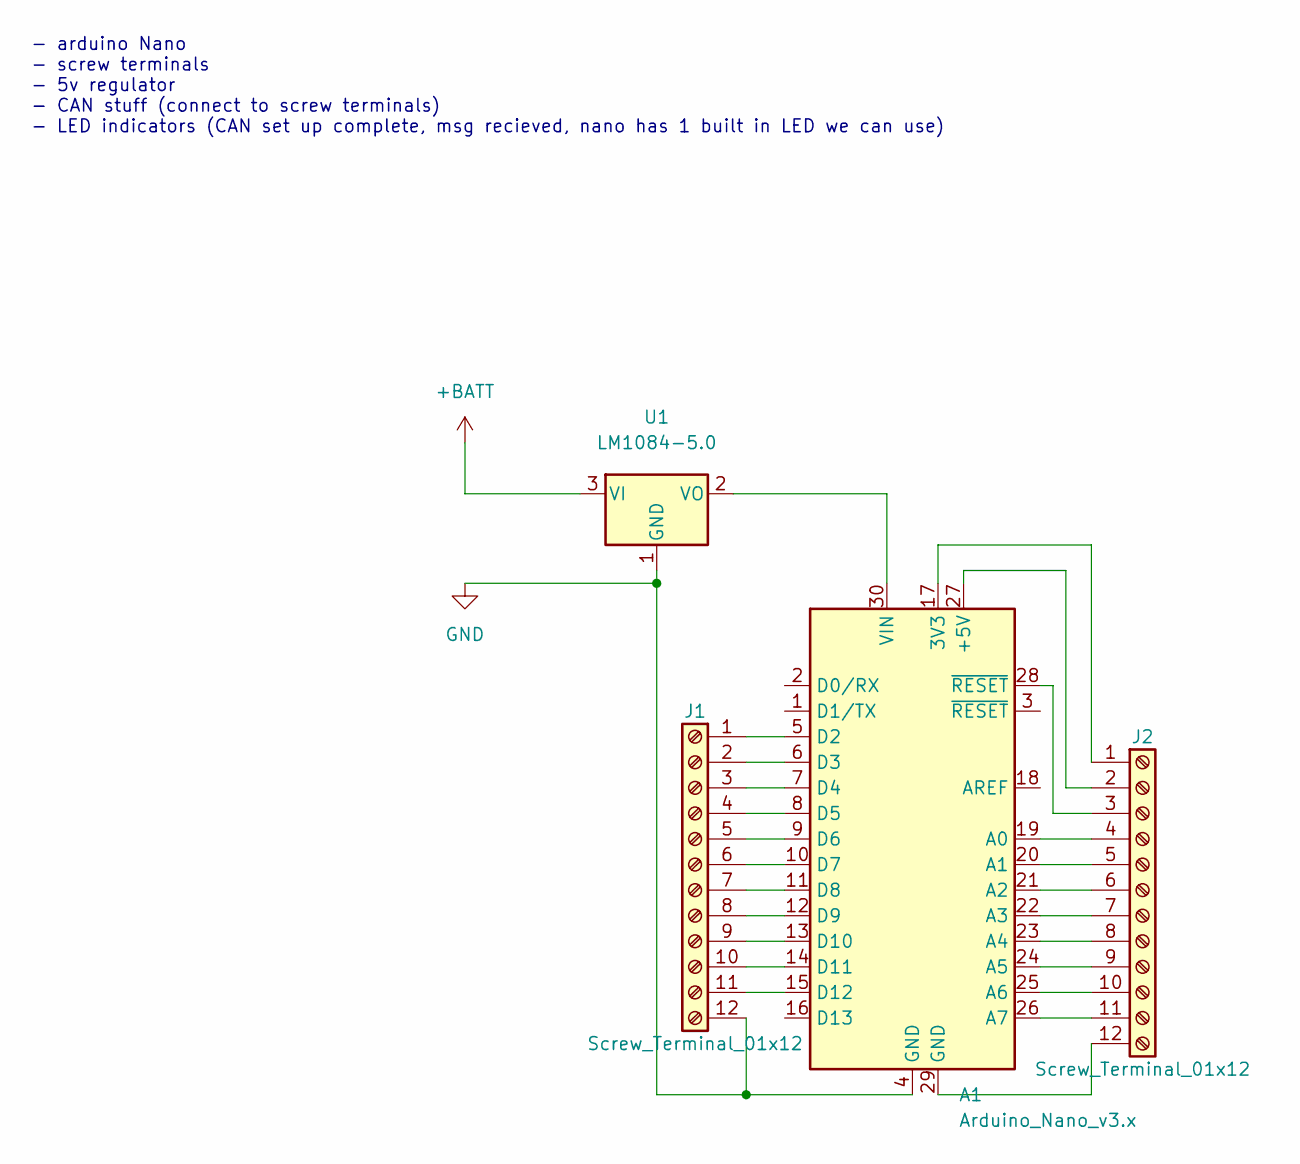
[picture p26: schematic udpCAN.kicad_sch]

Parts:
A1: Arduino_Nano_v3.x; Arduino_Nano
J1, J2: Screw_Terminal_01x12; TerminalBlock_4Ucon_1x12_P3.50mm_Horizontal
U1: LM1084-5.0; TO-220F-3_Horizontal_TabDown

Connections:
+BATT: U1.3 (VI)
GND: A1.4 (GND), J1.12, U1.1 (GND)
unnamed: A1.5 (D2), J1.1
unnamed: A1.6 (D3), J1.2
unnamed: A1.7 (D4), J1.3
unnamed: A1.8 (D5), J1.4
unnamed: A1.9 (D6), J1.5
unnamed: A1.10 (D7), J1.6
unnamed: A1.11 (D8), J1.7
unnamed: A1.12 (D9), J1.8
unnamed: A1.13 (D10), J1.9
unnamed: A1.14 (D11), J1.10
unnamed: A1.15 (D12), J1.11
unnamed: A1.17 (3V3), J2.1
unnamed: A1.19 (A0), J2.4
unnamed: A1.20 (A1), J2.5
unnamed: A1.21 (A2), J2.6
unnamed: A1.22 (A3), J2.7
unnamed: A1.23 (A4), J2.8
unnamed: A1.24 (A5), J2.9
unnamed: A1.25 (A6), J2.10
unnamed: A1.26 (A7), J2.11
unnamed: A1.27 (+5V), J2.2
unnamed: A1.28 (~RESET), J2.3
unnamed: A1.29 (GND), J2.12
unnamed: A1.30 (VIN), U1.2 (VO)

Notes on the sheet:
- arduino Nano - screw terminals - 5v regulator - CAN stuff (connect to screw terminals) - LED indicators (CAN set up complete, msg recieved, nano has 1 built in LED we can use)

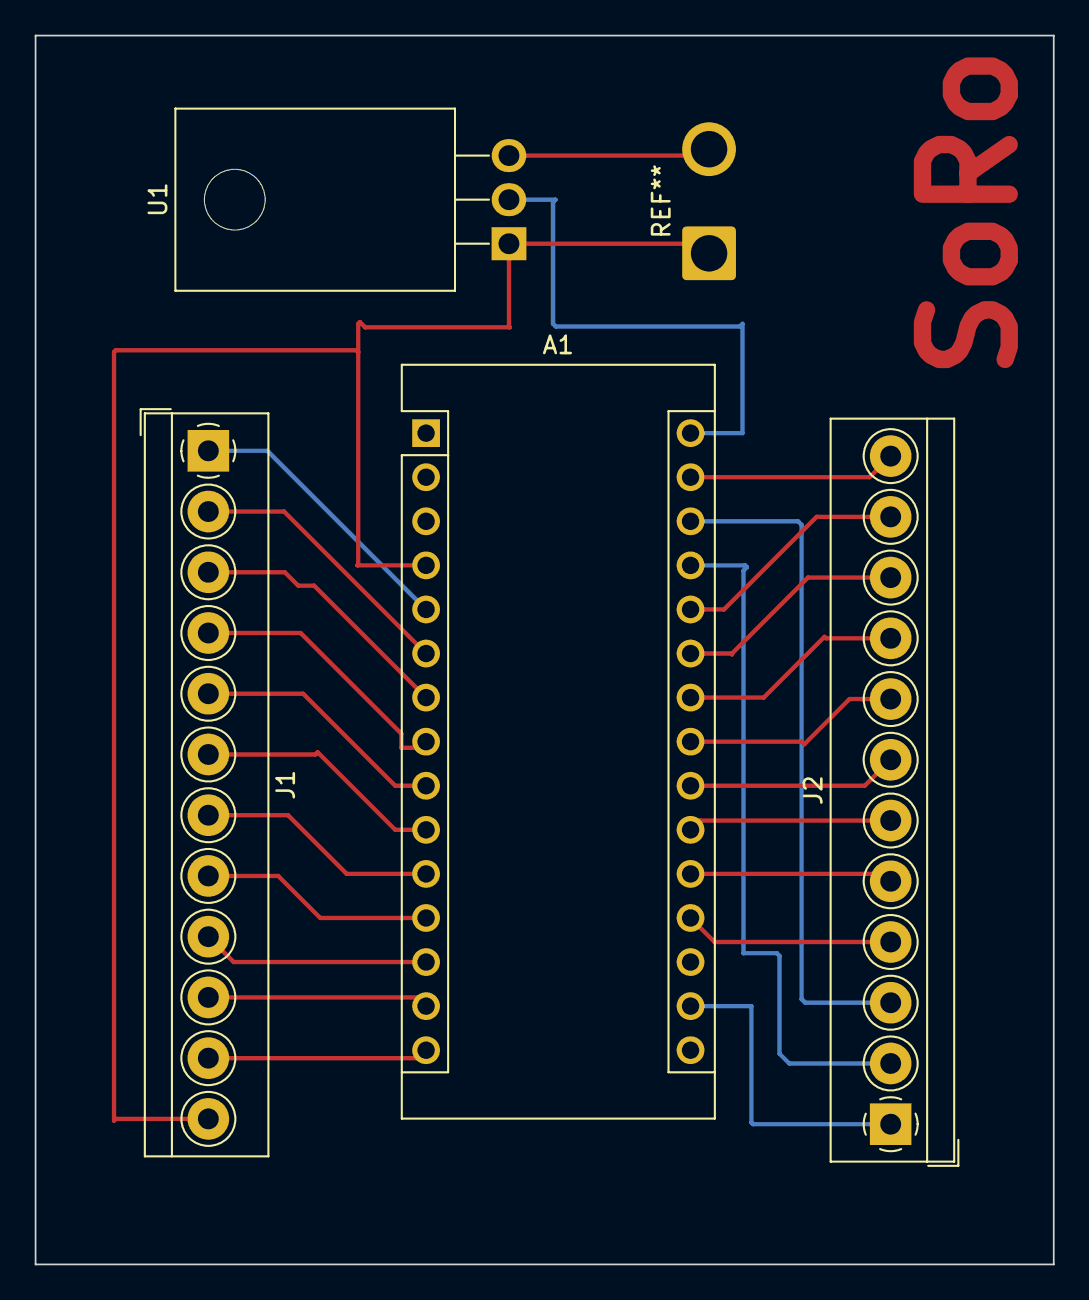
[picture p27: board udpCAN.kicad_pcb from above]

Board: 2 copper layers, 58.7 x 70.8 mm, 4 parts (0 on the bottom side), 25 nets.

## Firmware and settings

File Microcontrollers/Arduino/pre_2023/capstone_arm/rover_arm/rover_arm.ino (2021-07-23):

#include <Ethernet.h>
#include <EthernetUdp.h>
#include <Servo.h>
#include "PID.h"

// "PID.h" is a modified version of Brett Beauregard's PID Library (see links below).
// https://playground.arduino.cc/Code/PIDLibrary/
// https://github.com/br3ttb/Arduino-PID-Library/
// All I did was add a function to reset the integral term.

// Advanced PID Rover Arm Tester (incomplete)
// Written for the Arduino Mega on the rover's arm
// Open the serial monitor to use

// This program lets you set manually set the position of each joint.
// Talons should be calibrated to the range of servo inputs 10-170.
// A position of 0 encoder ticks should be the default position.

// Caution: This code will not stop you from breaking the arm


// TODO: communication timeout
// TODO: figure out whether or not the program is crashing
// TODO: (not urgent) Increase precision of encoders

// need to test: actually using doubles for the PID stuff (improves accuracy)
//               limited max joint speed (by changing PID bounds)


// Arduino Mega pins to attach Talon controllers to
#define PIN_S_BASE 30
#define PIN_S_SHOULDER 31
#define PIN_S_ELBOW 32
#define PIN_S_CLAW 33
#define PIN_S_WRISTP 34
#define PIN_S_WRISTR 35

// Arduino Mega pins to attach limit switches to
#define PIN_L_BASE 36
#define PIN_L_SHOULDER_MIN 37
#define PIN_L_SHOULDER_MAX 38
#define PIN_L_ELBOW_MIN 39
#define PIN_L_ELBOW_MAX 40
#define PIN_L_WRISTP_MIN 41 // unused?
#define PIN_L_WRISTP_MAX 42 // unused?
#define PIN_L_CLAW 43

// Port K bits (pins) for encoders
#define ENC_BASE_A 0x01     // pin A8
#define ENC_BASE_B 0x02     // pin A9
#define ENC_SHOULDER_A 0x04 // pin A10
#define ENC_SHOULDER_B 0x08 // pin A11
#define ENC_ELBOW_A 0x10    // pin A12
#define ENC_ELBOW_B 0x20    // pin A13
#define ENC_WRISTP_A 0x40   // pin A14
#define ENC_WRISTP_B 0x80   // pin A15

// Encoder position limits
#define MIN_BASE -500          // update this!
#define MAX_BASE 500           // update this!
#define MIN_SHOULDER 0
#define MAX_SHOULDER 1100
#define MIN_ELBOW 0
#define MAX_ELBOW 310
#define MIN_WRISTP -278
#define MAX_WRISTP 295

// Offset of the setpoint for the PID controls during the zeroing process
#define ZERO_SPEED 10
// Time (ms) between changing encoder position
#define ZERO_PERIOD 500
#define DEBUG_PERIOD 750

#define PID_MAP_SERVO 255 // "PID range." If you change this, then you'll have to retune all PID loops
#define PID_LIMIT 200 // setting PID_LIMIT < PID_MAP_SERVO will cap the PID speeds w/o changing tuning

#define JOY_DEADZONE 20
#define JOY_MAX 863
#define JOY_ZERO 429
#define JOY_MIN 0

#define DEVICE_ID 1

// encoder positions - updated by interrupt
volatile int eBase = 0;
volatile int eShoulder = 0;
volatile int eElbow = 0;
volatile int eWristP = 0;
volatile byte port_k_prev = 0x00; // only used by ISR

// servo objects
Servo sBase;
Servo sShoulder;
Servo sElbow;
Servo sClaw;
Servo sWristP;
Servo sWristR;

// PID stuff
double pidSetBase, pidInBase, pidOutBase;
PID pidBase(&pidInBase, &pidOutBase, &pidSetBase, 1, 1, 0, P_ON_E, REVERSE); // numbers are P, I, D

double pidSetShoulder, pidInShoulder, pidOutShoulder;
PID pidShoulder(&pidInShoulder, &pidOutShoulder, &pidSetShoulder, 1, 1, 0, P_ON_E, REVERSE); // numbers are P, I, D

double pidSetElbow, pidInElbow, pidOutElbow;
PID pidElbow(&pidInElbow, &pidOutElbow, &pidSetElbow, 1, 1, 0, P_ON_E, REVERSE); // numbers are P, I, D

double pidSetWristP, pidInWristP, pidOutWristP;
PID pidWristP(&pidInWristP, &pidOutWristP, &pidSetWristP, 1, 1, 0, P_ON_E, REVERSE); // numbers are P, I, D

// UDP Stuff
char message[30];  // buffer to hold incoming packet
int messageSize;
EthernetUDP Udp;
static byte mymac[] = { 0xAB, 0xCD, 0xEF, 0x01, 0x23, 0x45 };
IPAddress myip(192, 168, 1, 140);
const int localPort = 2040;

// test program vars
bool calibrated = true;
unsigned long timePrint, timeZero;
int jWristR;
bool bClawO, bClawC;


void setup() {
  // setup servos
  sBase.attach(PIN_S_BASE);
  sShoulder.attach(PIN_S_SHOULDER);
  sElbow.attach(PIN_S_ELBOW);
  sClaw.attach(PIN_S_CLAW);
  sWristP.attach(PIN_S_WRISTP);
  sWristR.attach(PIN_S_WRISTR);
  
  sBase.write(90);
  sShoulder.write(90);
  sElbow.write(90);
  sClaw.write(90);
  sWristP.write(90);
  sWristR.write(90);

  // setup encoder pins and interrupts
  cli();
  DDRK &= 0x00; // set encoder pins (all 8 port k bits) as inputs
  PORTK |= 0xFF; // enable pullups on encoder pins
  PCICR |= 0x04; // enable port K pin change interrupt
  PCMSK2 |= 0xFF; // enable interrupt for all port K pins
  sei();

  port_k_prev = PINK;

  // setup limit switch pins (uses pull up resistors)
  pinMode(PIN_L_BASE, INPUT);
  digitalWrite(PIN_L_BASE, HIGH);
  pinMode(PIN_L_SHOULDER_MIN, INPUT);
  digitalWrite(PIN_L_SHOULDER_MIN, HIGH);
  pinMode(PIN_L_SHOULDER_MAX, INPUT);
  digitalWrite(PIN_L_SHOULDER_MAX, HIGH);
  pinMode(PIN_L_ELBOW_MIN, INPUT);
  digitalWrite(PIN_L_ELBOW_MIN, HIGH);
  pinMode(PIN_L_ELBOW_MAX, INPUT);
  digitalWrite(PIN_L_ELBOW_MAX, HIGH);
  pinMode(PIN_L_WRISTP_MIN, INPUT);
  digitalWrite(PIN_L_WRISTP_MIN, HIGH);
  pinMode(PIN_L_WRISTP_MAX, INPUT);
  digitalWrite(PIN_L_WRISTP_MAX, HIGH);
  pinMode(PIN_L_CLAW, INPUT);
  digitalWrite(PIN_L_CLAW, HIGH);
  
  // setup serial
  Serial.begin(9600);
  
  // setup PID stuff
  pidBase.SetOutputLimits(-PID_LIMIT, PID_LIMIT);
  pidInBase = mapD(eBase, MIN_BASE, MAX_BASE, -PID_LIMIT, PID_LIMIT);
  pidSetBase = mapD(0, MIN_BASE, MAX_BASE, -PID_LIMIT, PID_LIMIT);
  pidBase.SetSampleTime(10);
  pidBase.SetMode(AUTOMATIC);

  pidShoulder.SetOutputLimits(-PID_LIMIT, PID_LIMIT);
  pidInShoulder = mapD(eShoulder, MIN_SHOULDER, MAX_SHOULDER, -PID_LIMIT, PID_LIMIT);
  pidSetShoulder = mapD(0, MIN_SHOULDER, MAX_SHOULDER, -PID_LIMIT, PID_LIMIT);
  pidShoulder.SetSampleTime(10);
  pidShoulder.SetMode(AUTOMATIC);

  pidElbow.SetOutputLimits(-PID_LIMIT, PID_LIMIT);
  pidInElbow = mapD(eWristP, MIN_ELBOW, MAX_ELBOW, -PID_LIMIT, PID_LIMIT);
  pidSetElbow = mapD(0, MIN_ELBOW, MAX_ELBOW, -PID_LIMIT, PID_LIMIT);
  pidElbow.SetSampleTime(10);
  pidElbow.SetMode(AUTOMATIC);

  pidWristP.SetOutputLimits(-PID_LIMIT, PID_LIMIT);
  pidInWristP = mapD(eWristP, MIN_WRISTP, MAX_WRISTP, -PID_LIMIT, PID_LIMIT);
  pidSetWristP = mapD(0, MIN_WRISTP, MAX_WRISTP, -PID_LIMIT, PID_LIMIT);
  pidWristP.SetSampleTime(10);
  pidWristP.SetMode(AUTOMATIC);

  // setup ethernet/udp
  Ethernet.init(10);
  Ethernet.begin(mymac, myip);
  if (Ethernet.hardwareStatus() == EthernetNoHardware) {
    Serial.println("Ethernet shield was not found.  Sorry, can't run without hardware. :(");
    while (true) {
      delay(1); // do nothing, no point running without Ethernet hardware
    }
  }
  if (Ethernet.linkStatus() == LinkOFF) {
    Serial.println("Ethernet cable is not connected.");
  }
  Udp.begin(localPort);
}

/*
 * When a mesage is available, stor it in message[].
 * Returns true if it's a valid control message, otherwise false.
 */
bool verify_message()
{
  // (-127), Device ID (1), base (high), base (low),
  // shoulder (high), shoulder (low), elbow (high), elbow (low),
  // wrist pitch (high), wrist pitch (low),
  // wrist roll (joystick high), wrist roll (joystick low),
  // buttons, hash

  messageSize = Udp.parsePacket();
  if (messageSize == 0)
    return false;
  
  Udp.read(message, messageSize);

  /*
  // DEBUG:
  for (int i = 0; i < messageSize: i++)
  {
    Serial.print((int)(message[i]));
    Serial.print(", ");
  }
  Serial.print("\n");
  */
  
  if(messageSize != 14)
  {
    Serial.println("Message is wrong length!");
    return false;
  }

  if(message[0] != -127)
  {
    Serial.println("Message does not start with -127!");
    return false;
  }

  if(message[1] != 1)
  {
    Serial.println("Wrong device id!");
    return false;
  }
  
  char hash = (message[2] + message[3] + message[4] + message[5] + message[6] + message[7] + message[8] + message[9] + message[10] + message[11] + message[12]) / 11;
  if(hash != message[13])
  {
    Serial.println("Wrong hash!");
    return false;
  }

  return true;
}

/*
 * Same function as the built in map(), except for a couple differences:
 * Uses doubles to give the PID controllers more precision
 * Limits the output to not go past out_min or out_max
 */
double mapD(double x, double in_min, double in_max, double out_min, double out_max) {
  //return (double(x)-double(in_min)) * (double(out_max) - double(out_min)) / (double(in_max) - double(in_min)) + double(out_min);
  double temp;
  temp = (x-in_min) * (out_max - out_min) / (in_max - in_min) + out_min;
  if (temp > out_max)
    temp = out_max;
  else if (temp < out_min)
    temp = out_min;
  return temp;
}

/*
 * Sets all pid control setpoints and encoder positions to 0.
 * Stop motors.
 */
void pid_reset()
{
  sBase.write(90);
  eBase = 0;
  pidInBase = mapD(0, MIN_BASE, MAX_BASE, -PID_LIMIT, PID_LIMIT);
  pidSetBase = mapD(0, MIN_BASE, MAX_BASE, -PID_LIMIT, PID_LIMIT);
  pidBase.ResetI();
  
  sShoulder.write(90);
  eShoulder = 0;
  pidInShoulder = mapD(0, MIN_SHOULDER, MAX_SHOULDER, -PID_LIMIT, PID_LIMIT);
  pidSetShoulder = mapD(0, MIN_SHOULDER, MAX_SHOULDER, -PID_LIMIT, PID_LIMIT);
  pidShoulder.ResetI();

  sElbow.write(90);
  eElbow = 0;
  pidInElbow = mapD(0, MIN_ELBOW, MAX_ELBOW, -PID_LIMIT, PID_LIMIT);
  pidSetElbow = mapD(0, MIN_ELBOW, MAX_ELBOW, -PID_LIMIT, PID_LIMIT);
  pidElbow.ResetI();

  sWristP.write(90);
  eWristP = 0;
  pidInWristP = mapD(0, MIN_WRISTP, MAX_WRISTP, -PID_LIMIT, PID_LIMIT);
  pidSetWristP = mapD(0, MIN_WRISTP, MAX_WRISTP, -PID_LIMIT, PID_LIMIT);
  pidWristP.ResetI();
}

/*
 * Update pid controllers.
 * Handles limit switches.
 * Set motor speeds.
 * Doesn't change setpoints. 
 */
void pid_update()
{
  int temp;
  
  pidInBase = mapD(eBase, MIN_BASE, MAX_BASE, -PID_LIMIT, PID_LIMIT);
  pidBase.Compute();
  sBase.write(map(pidOutBase, -PID_MAP_SERVO, PID_MAP_SERVO, 10, 170));
  // TODO: limit switch(?)
  
  pidInShoulder = mapD(eShoulder, MIN_SHOULDER, MAX_SHOULDER, -PID_LIMIT, PID_LIMIT);
  pidShoulder.Compute();
  temp = map(pidOutShoulder, -PID_MAP_SERVO, PID_MAP_SERVO, 10, 170);
  if (digitalRead(PIN_L_SHOULDER_MIN) == LOW)
  {
    // limit switch pressed: reset position. don't let the motor move towards stow.
    eShoulder = MIN_SHOULDER;
    if (temp > 90)
      temp = 90;
  }
  if (digitalRead(PIN_L_SHOULDER_MAX) == LOW)
  {
    // limit switch pressed: reset position. don't let the motor move towards stow.
    eShoulder = MAX_SHOULDER;
    if (temp < 90)
      temp = 90;
  }
  sShoulder.write(temp);
  
  pidInElbow = mapD(eElbow, MIN_ELBOW, MAX_ELBOW, -PID_LIMIT, PID_LIMIT);
  pidElbow.Compute();
  temp = map(pidOutElbow, -PID_MAP_SERVO, PID_MAP_SERVO, 10, 170);
  if (digitalRead(PIN_L_ELBOW_MIN) == LOW)
  {
    // limit switch pressed: reset position. don't let the motor move towards stow.
    eElbow = MIN_ELBOW;
    if (temp > 90)
      temp = 90;
  }
  else if (digitalRead(PIN_L_ELBOW_MAX) == LOW)
  {
    // limit switch pressed: reset position. don't let the motor move towards stow.
    eElbow = MAX_ELBOW;
    if (temp < 90)
      temp = 90;
  }
  sElbow.write(temp);
  
  pidInWristP = mapD(eWristP, MIN_WRISTP, MAX_WRISTP, -PID_LIMIT, PID_LIMIT);
  pidWristP.Compute();
  sWristP.write(map(pidOutWristP, -PID_MAP_SERVO, PID_MAP_SERVO, 10, 170));
  // TODO: limit switch(?)
}

/* 
 * Moves all joints towards "zero" positions until the corresponding limit switch is pressed.
 * Needs to be called continuously until complete.
 * Currently only moves elbow and shoulder joints.
 */
void pid_zero() {
  // periodically add to encoder values to make joints move towards stow position.
  // set calibrated to true when complete
  if (millis()-timeZero > ZERO_PERIOD)
  {
    Serial.println("Zeroing...");
    timeZero = millis();
    calibrated = true;
    
    if (digitalRead(PIN_L_SHOULDER_MIN) == HIGH) // switch not pressed
    {
      eShoulder += ZERO_SPEED;
      calibrated = false;
    }

    if (digitalRead(PIN_L_ELBOW_MIN) == HIGH)
    {
      eElbow += ZERO_SPEED;
      calibrated = false;
    }
  }
}

void loop() {
  // periodically display encoder positions
  if (millis()-timePrint > DEBUG_PERIOD)
  {
    timePrint = millis();
    
    //Serial.println("set: " + String(pidSetShoulder) + "\tin: " + String(pidInShoulder) + "\tout: " + String(pidOutShoulder));
    
    /*
    Serial.print("B: " + String(pidSetBase) + ", " + String(pidOutBase));
    Serial.print("\tS: " + String(pidSetShoulder) + ", " + String(pidOutShoulder));
    Serial.print("\tE: " + String(pidSetElbow) + ", " + String(pidOutElbow));
    Serial.println("\tW: " + String(pidSetWristP) + ", " + String(pidOutWristP));
    */

    /*
    Serial.print("B: " + String(eBase));
    Serial.print("\tS: " + String(eShoulder));
    Serial.print("\tE: " + String(eElbow));
    Serial.println("\tW: " + String(eWristP));
    */
  }

  // update control variables when a message is received
  if (verify_message())
  {
    
    // DEBUG:
    for (int i = 0; i < messageSize; i++)
    {
      Serial.print((int)(message[i]));
      Serial.print(", ");
    }
    Serial.print("\n");
    

    double tempB, tempS, tempE, tempW;
    tempB = (double)((int)(message[2] << 8) + (byte)message[3]);
    tempS = (double)((int)(message[4] << 8) + (byte)message[5]);
    tempE = (double)((int)(message[6] << 8) + (byte)message[7]);
    tempW = (double)((int)(message[8] << 8) + (byte)message[9]);
    pidSetBase = mapD(tempB, MIN_BASE, MAX_BASE, -PID_LIMIT, PID_LIMIT);
    pidSetShoulder = mapD(tempS, MIN_SHOULDER, MAX_SHOULDER, -PID_LIMIT, PID_LIMIT);
    pidSetElbow = mapD(tempE, MIN_ELBOW, MAX_ELBOW, -PID_LIMIT, PID_LIMIT);
    pidSetWristP = mapD(tempW, MIN_WRISTP, MAX_WRISTP, -PID_LIMIT, PID_LIMIT);

    // wrist roll
    jWristR = ((int)(message[10] << 8) + (byte)message[11]);
    if (jWristR > JOY_MAX)
      jWristR = JOY_MAX;
    else if (jWristR < JOY_MIN)
      jWristR = JOY_MIN;
    if (jWristR > JOY_ZERO+JOY_DEADZONE)
      sWristR.write(map(jWristR, JOY_ZERO+JOY_DEADZONE, JOY_MAX, 90, 170));
    else if (jWristR < JOY_ZERO-JOY_DEADZONE)
      sWristR.write(map(jWristR, JOY_ZERO-JOY_DEADZONE, JOY_MIN, 90, 10));
    else
      sWristR.write(90);
    //Serial.println(sWristR.read());
      
  
    // open/close claw
    bClawO = (message[12] & 1);
    bClawC = ((message[12] >> 1) & 1);
    if (bClawO && !bClawC)
      sClaw.write(170);
    else if (bClawC && !bClawO)
      sClaw.write(10);
    else
      sClaw.write(90);
  }

  // update pid, motor outputs
  pid_update();

  if (!calibrated)
    pid_zero();
}

ISR(PCINT2_vect) // pin change interrupt for pins A8 to A15 (update encoder positions)
{
  byte port_k_pins = PINK;

  // base
  if ((port_k_pins & ENC_BASE_A) && !(port_k_prev & ENC_BASE_A)) // rising edge on A
  {
    if (port_k_pins & ENC_BASE_B)
      eBase--; // CCW
    else
      eBase++; // CW
  }
  else if (!(port_k_pins & ENC_BASE_A) && (port_k_prev & ENC_BASE_A)) // falling edge on A
  {
    if (port_k_pins & ENC_BASE_B)
      eBase++; // CW
    else
      eBase--; // CCW
  }

  // shoulder
  if ((port_k_pins & ENC_SHOULDER_A) && !(port_k_prev & ENC_SHOULDER_A)) // rising edge on A
  {
    if (port_k_pins & ENC_SHOULDER_B)
      eShoulder--; // CCW
    else
      eShoulder++; // CW
  }
  else if (!(port_k_pins & ENC_SHOULDER_A) && (port_k_prev & ENC_SHOULDER_A)) // falling edge on A
  {
    if (port_k_pins & ENC_SHOULDER_B)
      eShoulder++; // CW
    else
      eShoulder--; // CCW
  }

  // elbow
  if ((port_k_pins & ENC_ELBOW_A) && !(port_k_prev & ENC_ELBOW_A)) // rising edge on A
  {
    if (port_k_pins & ENC_ELBOW_B)
      eElbow--; // CCW
    else
      eElbow++; // CW
  }
  else if (!(port_k_pins & ENC_ELBOW_A) && (port_k_prev & ENC_ELBOW_A)) // falling edge on A
  {
    if (port_k_pins & ENC_ELBOW_B)
      eElbow++; // CW
    else
      eElbow--; // CCW
  }

  // wrist pitch
  if ((port_k_pins & ENC_WRISTP_A) && !(port_k_prev & ENC_WRISTP_A)) // rising edge on A
  {
    if (port_k_pins & ENC_WRISTP_B)
      eWristP--; // CCW
    else
      eWristP++; // CW
  }
  else if (!(port_k_pins & ENC_WRISTP_A) && (port_k_prev & ENC_WRISTP_A)) // falling edge on A
  {
    if (port_k_pins & ENC_WRISTP_B)
      eWristP++; // CW
    else
      eWristP--; // CCW
  }
  
  port_k_prev = port_k_pins;
}

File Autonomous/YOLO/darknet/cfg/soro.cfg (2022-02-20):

[net]
# Testing
#batch=1
#subdivisions=1
# Training
batch=32
subdivisions=16
width=608
height=608
channels=3
momentum=0.949
decay=0.0005
angle=0
saturation = 1.5
exposure = 1.5
hue=.1

learning_rate=0.001
burn_in=1000
max_batches = 6000
policy=steps
steps=4800,5400
scales=.1,.1

#cutmix=1
mosaic=1

#:104x104 54:52x52 85:26x26 104:13x13 for 416

[convolutional]
batch_normalize=1
filters=32
size=3
stride=1
pad=1
activation=mish

# Downsample

[convolutional]
batch_normalize=1
filters=64
size=3
stride=2
pad=1
activation=mish

[convolutional]
batch_normalize=1
filters=64
size=1
stride=1
pad=1
activation=mish

[route]
layers = -2

[convolutional]
batch_normalize=1
filters=64
size=1
stride=1
pad=1
activation=mish

[convolutional]
batch_normalize=1
filters=32
size=1
stride=1
pad=1
activation=mish

[convolutional]
batch_normalize=1
filters=64
size=3
stride=1
pad=1
activation=mish

[shortcut]
from=-3
activation=linear

[convolutional]
batch_normalize=1
filters=64
size=1
stride=1
pad=1
activation=mish

[route]
layers = -1,-7

[convolutional]
batch_normalize=1
filters=64
size=1
stride=1
pad=1
activation=mish

# Downsample

[convolutional]
batch_normalize=1
filters=128
size=3
stride=2
pad=1
activation=mish

[convolutional]
batch_normalize=1
filters=64
size=1
stride=1
pad=1
activation=mish

[route]
layers = -2

[convolutional]
batch_normalize=1
filters=64
size=1
stride=1
pad=1
activation=mish

[convolutional]
batch_normalize=1
filters=64
size=1
stride=1
pad=1
activation=mish

[convolutional]
batch_normalize=1
filters=64
size=3
stride=1
pad=1
activation=mish

[shortcut]
from=-3
activation=linear

[convolutional]
batch_normalize=1
filters=64
size=1
stride=1
pad=1
activation=mish

[convolutional]
batch_normalize=1
filters=64
size=3
stride=1
pad=1
activation=mish

[shortcut]
from=-3
activation=linear

[convolutional]
batch_normalize=1
filters=64
size=1
stride=1
pad=1
activation=mish

[route]
layers = -1,-10

[convolutional]
batch_normalize=1
filters=128
size=1
stride=1
pad=1
activation=mish

# Downsample

[convolutional]
batch_normalize=1
filters=256
size=3
stride=2
pad=1
activation=mish

[convolutional]
batch_normalize=1
filters=128
size=1
stride=1
pad=1
activation=mish

[route]
layers = -2

[convolutional]
batch_normalize=1
filters=128
size=1
stride=1
pad=1
activation=mish

[convolutional]
batch_normalize=1
filters=128
size=1
stride=1
pad=1
activation=mish

[convolutional]
batch_normalize=1
filters=128
size=3
stride=1
pad=1
activation=mish

[shortcut]
from=-3
activation=linear

[convolutional]
batch_normalize=1
filters=128
size=1
stride=1
pad=1
activation=mish

[convolutional]
batch_normalize=1
filters=128
size=3
stride=1
pad=1
activation=mish

[shortcut]
from=-3
activation=linear

[convolutional]
batch_normalize=1
filters=128
size=1
stride=1
pad=1
activation=mish

[convolutional]
batch_normalize=1
filters=128
size=3
stride=1
pad=1
activation=mish

[shortcut]
from=-3
activation=linear

[convolutional]
batch_normalize=1
filters=128
size=1
stride=1
pad=1
activation=mish

[convolutional]
batch_normalize=1
filters=128
size=3
stride=1
pad=1
activation=mish

[shortcut]
from=-3
activation=linear


[convolutional]
batch_normalize=1
filters=128
size=1
stride=1
pad=1
activation=mish

[convolutional]
batch_normalize=1
filters=128
size=3
stride=1
pad=1
activation=mish

[shortcut]
from=-3
activation=linear

[convolutional]
batch_normalize=1
filters=128
size=1
stride=1
pad=1
activation=mish

[convolutional]
batch_normalize=1
filters=128
size=3
stride=1
pad=1
activation=mish

[shortcut]
from=-3
activation=linear

[convolutional]
batch_normalize=1
filters=128
size=1
stride=1
pad=1
activation=mish

[convolutional]
batch_normalize=1
filters=128
size=3
stride=1
pad=1
activation=mish

[shortcut]
from=-3
activation=linear

[convolutional]
batch_normalize=1
filters=128
size=1
stride=1
pad=1
activation=mish

[convolutional]
batch_normalize=1
filters=128
size=3
stride=1
pad=1
activation=mish

[shortcut]
from=-3
activation=linear

[convolutional]
batch_normalize=1
filters=128
size=1
stride=1
pad=1
activation=mish

[route]
layers = -1,-28

[convolutional]
batch_normalize=1
filters=256
size=1
stride=1
pad=1
activation=mish

# Downsample

[convolutional]
batch_normalize=1
filters=512
size=3
stride=2
pad=1
activation=mish

[convolutional]
batch_normalize=1
filters=256
size=1
stride=1
pad=1
activation=mish

[route]
layers = -2

[convolutional]
batch_normalize=1
filters=256
size=1
stride=1
pad=1
activation=mish

[convolutional]
batch_normalize=1
filters=256
size=1
stride=1
pad=1
activation=mish

[convolutional]
batch_normalize=1
filters=256
size=3
stride=1
pad=1
activation=mish

[shortcut]
from=-3
activation=linear


[convolutional]
batch_normalize=1
filters=256
size=1
stride=1
pad=1
activation=mish

[convolutional]
batch_normalize=1
filters=256
size=3
stride=1
pad=1
activation=mish

[shortcut]
from=-3
activation=linear


[convolutional]
batch_normalize=1
filters=256
size=1
stride=1
pad=1
activation=mish
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

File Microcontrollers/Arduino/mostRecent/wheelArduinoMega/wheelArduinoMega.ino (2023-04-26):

/*
     Pin wiring diagram

     [],pin  front   [],pin
     0,2     0-|-0    3,11
               |
     1,9     0-|-0   -4,12
               |
    -2,20    0-|-0   -5,13
     "-" indicaes wheel's polarity needs to be reversed

     gimbal pan: D6
     gimbal tilt: D7

     LED RGB: 19,20,21

     Pins used by Ethernet:

*/

/*
 * STILL NEED TO ADD GPS
 */
#include <Ethernet.h>
#include <EthernetUdp.h>
#include <Servo.h>

// Enter a MAC address and IP address for your controller below.
// The IP address will be dependent on your local network:
byte mac[] = {0xDE, 0xAD, 0xBE, 0xEF, 0xFE, 0xED};
IPAddress ip(10, 0, 0, 101);

unsigned int localPort = 1001;      // local port to listen on

// buffers for receiving and sending data
char packetBuffer[UDP_TX_PACKET_MAX_SIZE];  // buffer to hold incoming packet,
char ReplyBuffer[] = "acknowledged";        // a string to send back

// An EthernetUDP instance to let us send and receive packets over UDP
EthernetUDP Udp;


#define DEBUG 1 // set to 0 to avoid compiling print statements (will save space, don't need to print if running on rover)
int checkSum = 0; // used to check for errors in recieved message.
#define greenPin 10 // LED pins
#define redPin 11
#define bluePin 12
#define LED 0x02
#define WHEEL 0x00


int vertPos = 90; // position of gimbal
int horizPos = 90; 

Servo wheel0, wheel1, wheel2, wheel3, wheel4, wheel5, gimbalVert, gimbalHoriz;
Servo wheels[6] = {wheel0, wheel1, wheel2, wheel3, wheel4, wheel5};
bool wheelReverse[6] = {true, false, false, true, false, true};
// PWM on mega is D2-D13. Using D8-13 for wheels, D7/D6 for gimbal, and D19/D20/D21 for LEDs

unsigned long timeOut = 0; // used to measure time between msgs. If we go a full second without new msgs, stop wheels so rover doesn't run away from us

// super awesome fun proportional wheel control variables
bool proportionalControl = true;
int targetSpeeds[6] = {126, 126, 126, 126, 126, 126};
double currentSpeeds[6] = {126, 126, 126, 126, 126, 126};

unsigned long lastLoop = 0; // milli time of last loop
double deltaLoop = 0.0; // seconds since last loop

double Kp = 1.0; // proportional change between target and current

double error[6];

// define time in microseconds of width of pulse
const int PWM_LOW = 1000;
const int PWM_HIGH = 2000;
const int PWM_NEUTRAL = 1500; 

void setup() {
  // You can use Ethernet.init(pin) to configure the CS pin
  //Ethernet.init(10);  // Most Arduino shields <---
  //Ethernet.init(5);   // MKR ETH Shield
  //Ethernet.init(0);   // Teensy 2.0
  //Ethernet.init(20);  // Teensy++ 2.0
  //Ethernet.init(15);  // ESP8266 with Adafruit FeatherWing Ethernet
  //Ethernet.init(33);  // ESP32 with Adafruit FeatherWing Ethernet
  wheel0.attach(2);
  wheel1.attach(3);
  wheel2.attach(4);
  wheel3.attach(5);
  wheel4.attach(6);
  wheel5.attach(7);

  gimbalVert.attach(8);
  gimbalHoriz.attach(9);

  pinMode(redPin, OUTPUT); // red
  pinMode(greenPin, OUTPUT); // green
  pinMode(bluePin, OUTPUT); // blue

  // start the Ethernet
  Ethernet.begin(mac, ip);

  // Open serial communications and wait for port to open:
  #if DEBUG
    Serial.begin(9600);
    while (!Serial) {
      ; // wait for serial port to connect. Needed for native USB port only
    }
  #endif

  // Check for Ethernet hardware present
  if (Ethernet.hardwareStatus() == EthernetNoHardware) {
    #if DEBUG
    Serial.println("Ethernet shield was not found.  Sorry, can't run without hardware. :(");
    #endif
    while (true) {
      delay(1); // do nothing, no point running without Ethernet hardware
    }
  }
  if (Ethernet.linkStatus() == LinkOFF) {
    #if DEBUG
    Serial.println("Ethernet cable is not connected.");
    #endif
  }

  // start UDP
  Udp.begin(localPort);
}

void updateGimbal(int vertical, int horizontal) {
  // inputs are 0 for counter-clockwise, 1 for nothing, 2 for clockwise
   switch(vertical){
      case 2: 
        if(vertPos >= 180){
          vertPos=179;
        }
        vertPos += 1; 
        break;
      case 0:
        if(vertPos <= 0){
          vertPos=1;
        }
        vertPos -= 1; 
        break;
   }
    switch(horizontal) {
      case 2: 
        if(horizPos >= 180){
          horizPos=179;
        }
        horizPos += 1; 
        break;
      case 0:
        if(horizPos <= 0){
          horizPos=1;
        }
        horizPos -= 1; 
        break;
      }
  gimbalVert.write(vertPos);
  gimbalHoriz.write(horizPos);
}

//LED msg: [0x23, 0x02, red, green, blue]
//WHEEL msg: [0x23, 0x00, w1, w2, w3, w4, w5, w6, checkSum]
void update(char msg[], int msgSize) {
  checkSum = 0;
  #if DEBUG
  //Serial.println("msg recieved:");
  for(int i=0; i<msgSize; ++i) {
    Serial.print(uint8_t(msg[i]));
    Serial.print(", ");
  }
  Serial.println();
  #endif
  
  if(msg[0] == 0x23) {
    /**************LED MSG *****************/
    if (msg[1] == LED) {
      if(msgSize == 5) {
        if(uint8_t(msg[2]) > 0) {
          digitalWrite(redPin, HIGH);
        }
        else {
          digitalWrite(redPin, LOW);
        }
        if(uint8_t(msg[3]) > 0) {
          digitalWrite(greenPin, HIGH);
        }
        else {
          digitalWrite(greenPin, LOW);
        }
        if(uint8_t(msg[4]) > 0) {
          digitalWrite(bluePin, HIGH);
        }
        else {
          digitalWrite(bluePin, LOW);
        }
      } 
      else {
        #if DEBUG
        Serial.println("msg for LEDS was wrong length... ignoring this message.");
        #endif
      }
    }
    /**************WHEEL MSG *****************/
    else if (msg[1] == WHEEL) {
      if(msgSize == 9) {
        for(int i=2; i<8; i++) { 
          checkSum += msg[i];
        }
        checkSum = checkSum & 0xff;
        #if DEBUG
          // Serial.print("Calcuated checksum: ");
          // Serial.println(checkSum);
          // Serial.print("Received checksum: ");
          // Serial.println((int)msg[8]);
        #endif
        if(checkSum == uint8_t(msg[8])) {
          timeOut = millis(); // save time so we know how long it's been between this and next msg
          // set the appropriate target speeds
          for (int i = 0; i < 6; i++) {
            targetSpeeds[i] = (uint8_t)msg[i+2];
          }          
          //updateGimbal(uint8_t(msg[8]), uint8_t(msg[9]));
        }
        else {
          #if DEBUG
          Serial.println("checkSum for WHEELS was incorrect... ignoring this message.");
          #endif
        }
      }
      else {
        #if DEBUG
        Serial.println("msg for WHEELS was wrong length... ignoring this message.");
        #endif
      }
    }
    else {
      #if DEBUG
      Serial.println("msg was for the wrong device... ignoring this message.");
      #endif
    }
  }
  else {
    #if DEBUG
    Serial.println("startByte was incorrect... ignoring this message.");
    #endif
  }
}

double clip(double value, double low, double high) {
  if (value < low) value = low;
  if (value > high) value = high;
  return value;
}
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

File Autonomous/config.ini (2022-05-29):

[CONFIG]
SWIFT_IP=10.0.0.222
SWIFT_PORT=55556
MBED_IP=10.0.0.101
MBED_PORT=1001
[ARTRACKER]
#dpp is .040625 with logi
DEGREES_PER_PIXEL=0.09375
VDEGREES_PER_PIXEL = .125
#Focal length was 1500 with logi
FOCAL_LENGTH=435
FOCAL_LENGTH30H=590
FOCAL_LENGTH30V=470
KNOWN_TAG_WIDTH=20
FORMAT=MJPG
FRAME_WIDTH=1280
FRAME_HEIGHT=720
MAIN_CAMERA=2.3
LEFT_CAMERA=2.4
RIGHT_CAMERA=2.2
[YOLO]
#I am assuming that these are in the darknet folder
WEIGHTS=soro.weights
DATA=cfg/soro.data
CFG=cfg/soro.cfg
THRESHOLD=.25

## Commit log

2021-09-23 added constant to determine how many cameras to open
2021-09-24 at least it builds and runs, don't know if it works yet
    [config.txt]
2021-09-24 Revert "Bentongpsstuff"
    [config.txt]
2021-10-20 changed file structure, removed files not related to SWIG wrapping, updated README
    [config.txt]
2021-11-09 fix threading and imports
2021-12-20 Reorganized some stuff, added an ar example program and fix a ton of ar errors
    [config.ini]
2021-12-22 Cleaned up the print tags
2022-01-02 Fixed the run script, main.py now takes the cameras as a parameter, fixed small error in drive
2022-01-15 Code pretty much works with YOLO now but is far too slow. Should be fixable with GPU and yolo-lite. User must recompile and download the weights before this will run
    [config.ini]
2022-01-16 Adding .cfg files, the .name file and the image path files
    [soro-tiny.cfg, soro.cfg, yolov4-custom.cfg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]
2022-01-26 uploaded current code
2022-01-26 Added wheel MBED code
2022-01-26 Add files via upload
    Fixed the handling of signed inputs and the range so that it now takes inputs in the range -126 to 126.
    [main.cpp]
2022-01-26 Updated WheelMbed
    (Same as last commit) Fixed the handling of signed inputs and the range to take inputs from -126 to 126.
2022-02-07 made function in location.py that takes bearing and distance but returns coordinates, and made comments to clarify functionality.
2022-02-15 wheels move correctly
2022-02-18 Created location method that finds lat and long given bearing and distance
2022-02-19 Modded the checklist a bit and sending proper wheel speeds now
2022-02-19 fixed wheel speeds
2022-02-19 Print out the speeds in the setup drive
2022-02-19 Changes at the end of the first test day. Fixed a ton of bugs and chagned speeds to a tuple for some reason
    [config.ini]
2022-02-21 added front and back wheel drive to manual control
2022-02-21 The jetson libraries do not compile on the jetson so I'm not including them. As a result, if you try to use yolo now, it will fail
2022-02-23 added function in UDPOut to send LED colors
2022-02-23 added an executable for the arm code built for 64 bit windows
2022-02-23 maybe fixed arm code executable
2022-02-25 integrated old arm code into manual_operate (crying emoji)
2022-02-25 fixed more portions of arm code
2022-02-27 updated arm control scheme
2022-02-27 removed useless qt arm code
2022-02-27 Added led code and ensured user gives a camera when calling main
2022-03-02 trying to draw cool stuff w arm
2022-05-16 Fixed many of the autonomous pathing issues and implimented the final programs for the map
    [config.ini]
2022-05-27 fixed operation config file
    [config.ini]
2022-05-28 added new claw control
2022-05-29 leds flash now
2022-05-29 manual operation LEDs comply with URC rules
2022-06-03 fixed arm pins and added science gui
    [arm_controller.ino, config.ini]
2022-12-22 Added motors to lowerArm, just needs CAN receive implementation
2022-12-22 Wrote basis of upperArm code, still needs CAN and PID implementation
2023-01-02 Created blank PCB files for the Arm
    [Ebox-B_Cu.gbr, Ebox-B_Mask.gbr, Ebox-B_Paste.gbr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]
2023-01-02 Created the basis of each PCB, mainly just needs CAN/ LED indicators on each
    [lowerArm.kicad_pcb, lowerArm.kicad_sch, udpCAN.kicad_pcb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]
2023-02-09 changed makefile for jetson nano
2023-02-15 updated Arm arduino code, manual_operate, and PCBs
    [Ebox-B_Cu.gbr, Ebox-B_Mask.gbr, Ebox-B_Paste.gbr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]
2023-02-21 fixed camera arg parsing
2023-02-25 Updated wheel code, organized, added a folder for examples I'vemade
    [lowerArm-B_Cu.gbr, lowerArm-B_Mask.gbr, lowerArm-B_Paste.gbr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]
2023-02-26 Updated Arduino README.. still needs more
    [Science-B_Cu.gbr, Science-B_Mask.gbr, Science-B_Paste.gbr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]
2023-02-26 fixed checksum bug in manual_operate
    [wheelArduinoMega.ino]
2023-02-26 added proportional control to wheels
2023-02-28 fixed science package jittering
    [ScienceArduinoNano.ino]
2023-04-16 Added Teensy programs to Microcontrollers folder
    [lowerArm-B_Cu.gbr, lowerArm-B_Mask.gbr, lowerArm-B_Paste.gbr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]
2023-04-20 Finished the Teensy code and new_maual_operate code to function together on rover
2023-04-26 Added pictures of Arm to GUI and updated draw_arm_stuff to properly animate the images
2023-05-20 fixed bug where rover wouldn't auto stop
    [teensyEBOX.ino]
2023-05-20 Updated speeds on arm motors
2023-06-15 Fixed the bot .......
    [config.ini]
2023-09-21 fix: Clean up NTFS file names
    Because previous developers were using Windows to develop their project,
    they accidentally forgot that most systems have case-sensitive
    filesystems.
    This commit cleans up some of the messy filenames and adds 'correct'
    path strings. It also changes the path in `util.py` juuust in-case.
    Go ahead and use `git pull` to grab the new changes on the Raspberry Pi!
    :)
